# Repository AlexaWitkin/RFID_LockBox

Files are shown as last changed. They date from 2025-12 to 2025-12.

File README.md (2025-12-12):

# RFID_LockBox
### Abstract 
This project presents the design and implementation of a compact RFID-controlled lockbox intended to provide secure personal storage for an end user sharing a living space with a roommate. The goal was to create a reliable, stand-alone access-control system while gaining hands-on experience working with the ATmega328P as a discrete microcontroller rather than relying on a full Arduino development board. The system integrates an RC522 RFID reader operating at 13.56 MHz, a custom-designed PCB incorporating power regulation, logic-level shifting, and microcontroller support circuitry, and a servo-based mechanical locking mechanism housed within a laser-cut wooden enclosure. Throughout development, particular attention was given to power constraints, signal-integrity challenges between 5V and 3.3V domains, and practical issues such as servo initialization and UID formatting. The final design successfully demonstrates a functional, durable lockbox that reliably authenticates RFID tags and actuates a locking mechanism, achieving the project’s objectives in both usability and technical learning.

** For more information view 'CMPE 3185 Final Project.pdf'

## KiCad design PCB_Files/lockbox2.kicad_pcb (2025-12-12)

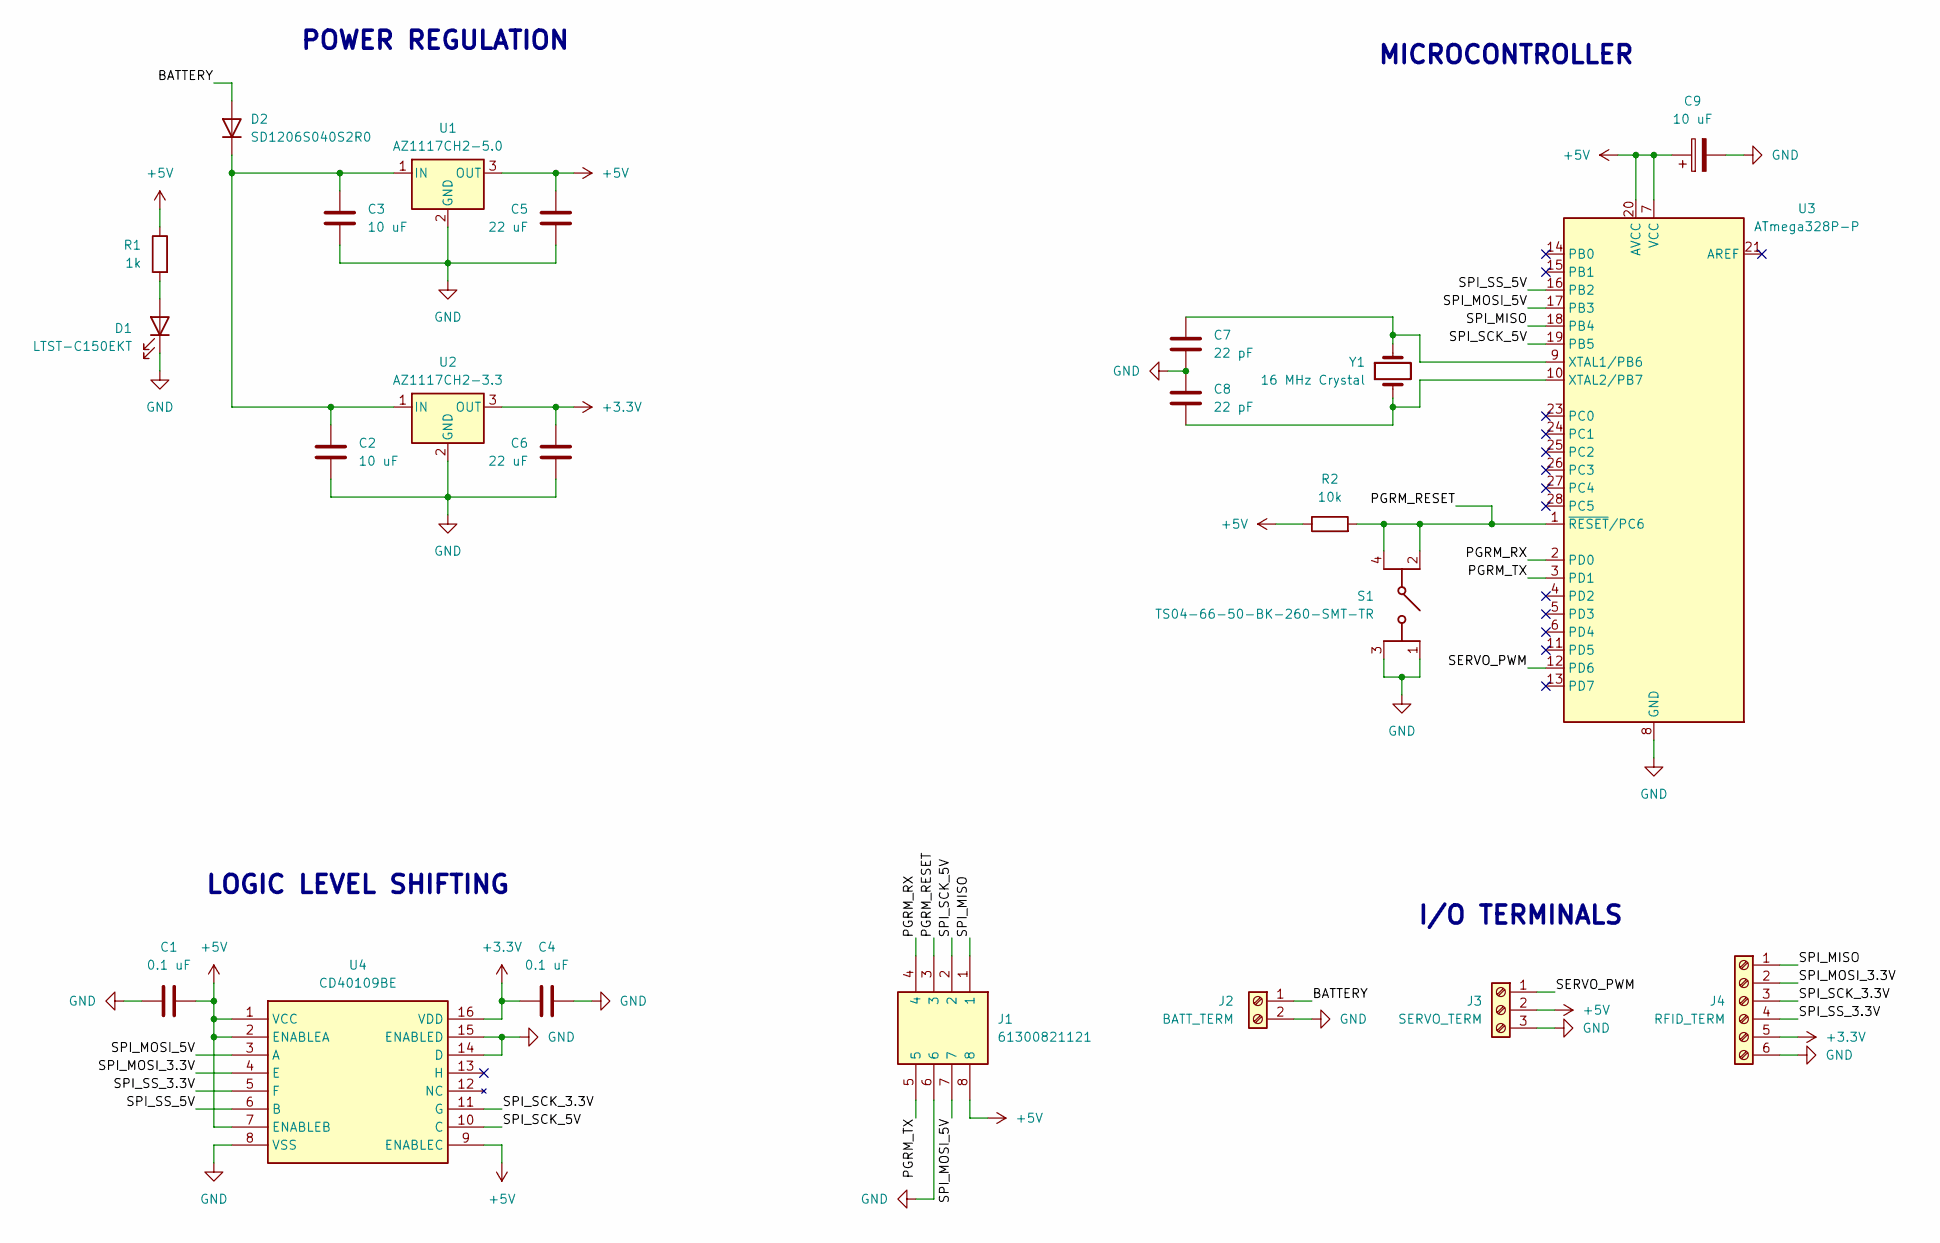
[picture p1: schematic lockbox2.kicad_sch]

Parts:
C1, C4: 0.1 uF; C_1206_3216Metric_Pad1.33x1.80mm_HandSolder
C2, C3: 10 uF; C_1206_3216Metric_Pad1.33x1.80mm_HandSolder
C5, C6: 22 uF; C_1206_3216Metric_Pad1.33x1.80mm_HandSolder
C7, C8: 22 pF; C_1206_3216Metric_Pad1.33x1.80mm_HandSolder
C9: 10 uF; CP_Radial_D5.0mm_P2.00mm
D1: LTST-C150EKT; LED_1206_3216Metric_Pad1.42x1.75mm_HandSolder
D2: SD1206S040S2R0; D_1206_3216Metric_Pad1.42x1.75mm_HandSolder
J1: 61300821121; Manufacturer_Part_Number 61300821121; Mouser Part Number 710-61300821121
J2: BATT_TERM; TerminalBlock_Phoenix_PT-1,5-2-5.0-H_1x02_P5.00mm_Horizontal
J3: SERVO_TERM; TerminalBlock_Phoenix_PT-1,5-3-5.0-H_1x03_P5.00mm_Horizontal
J4: RFID_TERM; TerminalBlock_Phoenix_PT-1,5-6-5.0-H_1x06_P5.00mm_Horizontal
R1: 1k; R_1206_3216Metric_Pad1.30x1.75mm_HandSolder
R2: 10k; R_1206_3216Metric_Pad1.30x1.75mm_HandSolder
S1: TS04-66-50-BK-260-SMT-TR; TS046650BK260SMTTR; Manufacturer_Part_Number TS04-66-50-BK-260-SMT-TR; Mouser Part Number 179-TS046650BK260SMR
U1: AZ1117CH2-5.0; SOT-223-3_TabPin2
U2: AZ1117CH2-3.3; SOT-223-3_TabPin2
U3: ATmega328P-P; DIP-28_W7.62mm
U4: CD40109BE; DIP794W53P254L1930H508Q16N; Manufacturer_Part_Number CD40109BE; Mouser Part Number 595-CD40109BE
Y1: 16 MHz Crystal; Crystal_HC49-U_Vertical

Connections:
+3.3V: C4.1, C6.1, J4.5, U2.3 (OUT), U4.16 (VDD)
+5V: C1.2, C5.1, C9.1, J1.8, J3.2, R1.1, R2.1, U1.3 (OUT), U3.7 (VCC), U3.20 (AVCC), U4.1 (VCC), U4.2 (ENABLEA), U4.7 (ENABLEB), U4.9 (ENABLEC)
/BATTERY: D2.2 (A), J2.1
/PGRM_RESET: J1.3, R2.2, S1.2 (COM_1), S1.4 (COM_2), U3.1 (~RESET/PC6)
/PGRM_RX: J1.4, U3.2 (PD0)
/PGRM_TX: J1.5, U3.3 (PD1)
/SERVO_PWM: J3.1, U3.12 (PD6)
/SPI_MISO: J1.1, J4.1, U3.18 (PB4)
/SPI_MOSI_3.3V: J4.2, U4.4 (E)
/SPI_MOSI_5V: J1.7, U3.17 (PB3), U4.3 (A)
/SPI_SCK_3.3V: J4.3, U4.11 (G)
/SPI_SCK_5V: J1.2, U3.19 (PB5), U4.10 (C)
/SPI_SS_3.3V: J4.4, U4.5 (F)
/SPI_SS_5V: U3.16 (PB2), U4.6 (B)
GND: C1.1, C2.2, C3.2, C4.2, C5.2, C6.2, C7.2, C8.1, C9.2, D1.1 (K), J1.6, J2.2, J3.3, J4.6, S1.1 (NO_1), S1.3 (NO_2), U1.2 (GND), U2.2 (GND), U3.8 (GND), U3.22 (GND), U4.8 (VSS), U4.14 (D), U4.15 (ENABLED)
unnamed: D1.2 (A), R1.2
unnamed: C2.1, C3.1, D2.1 (K), U1.1 (IN), U2.1 (IN)
unnamed: C7.1, U3.9 (XTAL1/PB6), Y1.1
unnamed: C8.2, U3.10 (XTAL2/PB7), Y1.2

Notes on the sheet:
I/O TERMINALS
MICROCONTROLLER
POWER REGULATION
LOGIC LEVEL SHIFTING

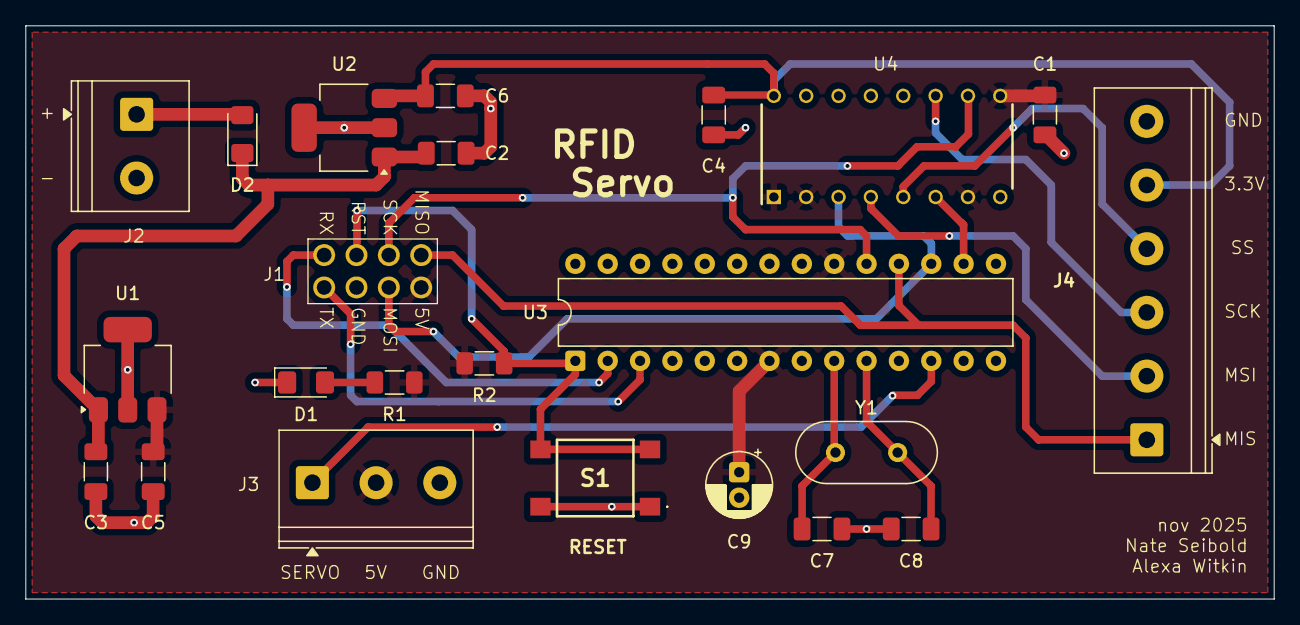
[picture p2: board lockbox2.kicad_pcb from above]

Board: 2 copper layers, 98.0 x 45.0 mm, 23 parts (0 on the bottom side), 19 nets.

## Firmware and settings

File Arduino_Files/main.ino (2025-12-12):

// Alexa Witkin 
// Nov 16. 2025
// Main for CMPE3815 - Lock

#include <SPI.h>
#include <MFRC522.h>
#include <Servo.h>

// ======== RFID ======== //
#define RST_PIN         9          // Configurable, see typical pin layout above
#define SS_PIN          10         // Configurable, see typical pin layout above

MFRC522 rfid(SS_PIN, RST_PIN);  // Create MFRC522 instance
String uid = ""; // Init string that will store new NUID 

const String validID = "201831131";


// ======== SERVO ======== //
Servo lock; // create servo object for lock 
//int lockPos = 0; // variable to store position of Lock Servo

void setup() {
	Serial.begin(9600);		// Initialize serial communications with the PC
	SPI.begin();			// Init SPI bus
	rfid.PCD_Init();		// Init MFRC522
	delay(4);				// Optional delay. Some board do need more time after init to be ready, see Readme
  Serial.println(F("This code scan the MIFARE Classsic NUID."));

  lock.attach(6); // lock is in pin D10
}

void loop() {
	//uid = "";
	//Serial.println(getUID());
	if (getUID() == validID) {
		Serial.println("Servo running");
		servoFunction();
	}
}
//201831131

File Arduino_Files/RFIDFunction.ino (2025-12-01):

/* This is a MFRC522 library example; for further details and other examples see: https://github.com/miguelbalboa/rfid
 * Typical pin layout used:
 * -----------------------------------------------------------------------------------------
 *             MFRC522      Arduino       Arduino   Arduino    Arduino          Arduino
 *             Reader/PCD   Uno/101       Mega      Nano v3    Leonardo/Micro   Pro Micro
 * Signal      Pin          Pin           Pin       Pin        Pin              Pin
 * -----------------------------------------------------------------------------------------
 * RST/Reset   RST          9             5         D9         RESET/ICSP-5     RST
 * SPI SS      SDA(SS)      10            53        D10        10               10
 * SPI MOSI    MOSI         11 / ICSP-4   51        D11        ICSP-4           16
 * SPI MISO    MISO         12 / ICSP-1   50        D12        ICSP-1           14
 * SPI SCK     SCK          13 / ICSP-3   52        D13        ICSP-3           15
 *
 * More pin layouts for other boards can be found here: https://github.com/miguelbalboa/rfid#pin-layout
 */

String getUID() {
  uid = "";
  delay(1000);
    // Reset the loop if no new card present on the sensor/reader. This saves the entire process when idle.
  if ( ! rfid.PICC_IsNewCardPresent())
    return "123456789";
  
  // Verify if the NUID has been readed
  if ( ! rfid.PICC_ReadCardSerial()) {
    return "123456789";
  }
  
  // Serial.print(F("PICC type: "));
  MFRC522::PICC_Type piccType = rfid.PICC_GetType(rfid.uid.sak);
  // Serial.println(rfid.PICC_GetTypeName(piccType));

  // Check is the PICC of Classic MIFARE type
  if (piccType != MFRC522::PICC_TYPE_MIFARE_MINI &&  
    piccType != MFRC522::PICC_TYPE_MIFARE_1K &&
    piccType != MFRC522::PICC_TYPE_MIFARE_4K) {
    Serial.println(F("Your tag is not of type MIFARE Classic."));
    return "000000000";
  }
  // Store NUID into string 
  for (byte i = 0; i < 4; i++) {
    uid += rfid.uid.uidByte[i];
  }

    // Serial.println(F("The NUID tag is:"));
    // Serial.println();
    // Serial.println(uid);

  // Halt PICC
  rfid.PICC_HaltA();

  // Stop encryption on PCD
  rfid.PCD_StopCrypto1();

  return uid;
}

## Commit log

2025-12-01 Added current working main and servo/rfid function files
2025-12-12 Files for PCB
    PCB files for manufacturing. Be aware, there are issues with the design that have not been fixed.
    [lockbox2.kicad_pcb, lockbox2.kicad_sch]
2025-12-12 delay 10 sec not 1 min + delete old version of function
    Updated delay duration and removed unused servo function.
2025-12-12 adding .svg files for laser cut boxes
2025-12-12 individual files moved to folders
    [lockbox2.kicad_pcb, lockbox2.kicad_sch]
